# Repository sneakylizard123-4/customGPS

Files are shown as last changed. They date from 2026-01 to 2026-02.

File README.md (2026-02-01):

# customGPS
A custom GPS and compass board for 5" drones.

## How to use
connect to power. GPS uses UART and compass uses I2C.
solder capacitor to "cap here"

# Pictures
blender render:


PCB:


Schematic:


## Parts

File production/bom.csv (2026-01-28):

Designator | Footprint | Quantity | Value | LCSC Part #
C1, C3, C4, C6 | 0805 | 4 | 100nF
C2, C7, C8 | 0805 | 3 | 1uF
C5 | 0805 | 1 | 10nF
D1, D2 | 0603 | 2 | Status LED
FB1 | 0603 | 1 | BLM18AG601SN1D | BLM18AG601SN1D
J1 | SolderWirePad_1x01_SMD_1x2mm | 1 | C+
J2 | SolderWirePad_1x01_SMD_1x2mm | 1 | C-
J3 | U.FL_Molex_MCRF_73412-0110_Vertical | 1 | U_FL-R-SMT-1_10_ | U.FL-R-SMT-1(10)
J4 | Hirose_DF13-06P-1.25DS_1x06_P1.25mm_Horizontal | 1 | To FC
J6 | SolderWirePad_1x01_SMD_1x2mm | 1 | DRDY
L1 | 0805 | 1 | 10nH
R1 | 0805 | 1 | 10k
R2, R3 | 0805 | 2 | 47
R4 | 0805 | 1 | 100
R5, R8 | 0805 | 2 | 1K
R6, R7 | 0805 | 2 | 0
TP1 | TestPoint_Pad_1.0x1.0mm | 1 | SAFEBOOT
TP2 | TestPoint_Pad_1.0x1.0mm | 1 | TimePulse
U1 | ublox_NEO | 1 | NEO-M8N
U2 | LGA-12_2x2mm_P0.5mm | 1 | LIS3MDL
U3 | SOT-23-5 | 1 | TLV75733PDBV

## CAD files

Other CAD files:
blender/customGPS.blend

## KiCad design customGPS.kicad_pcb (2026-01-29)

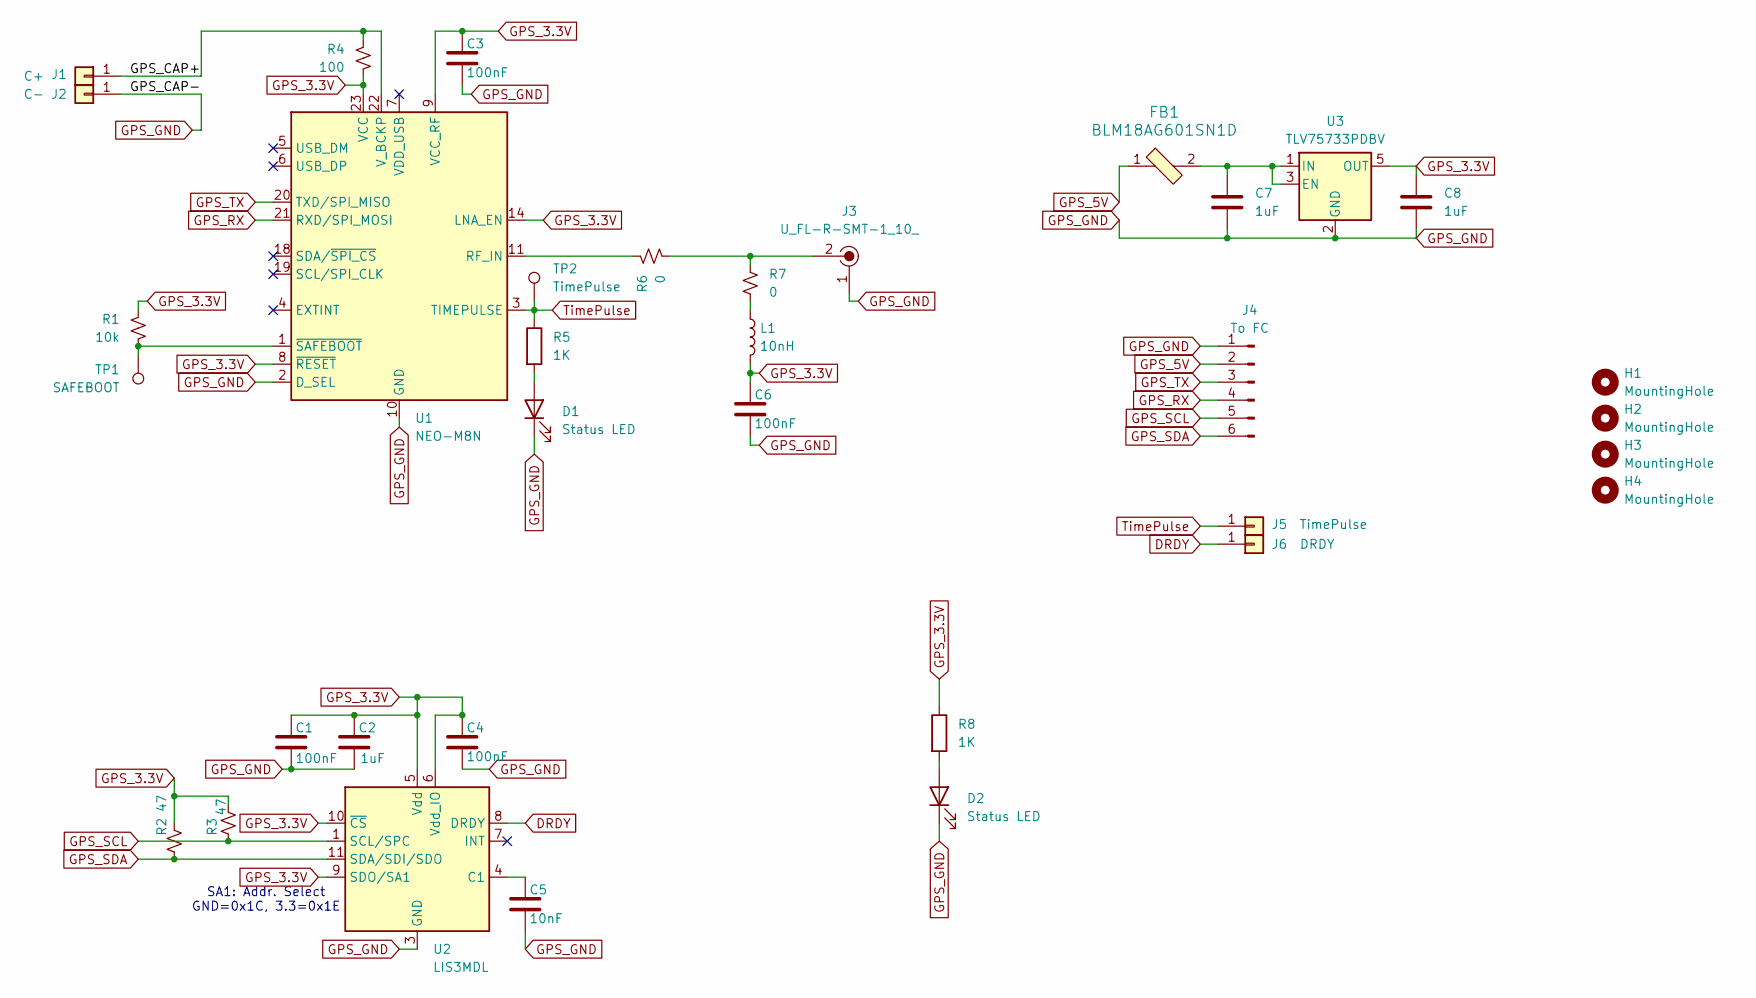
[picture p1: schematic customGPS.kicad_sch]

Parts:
C1, C3, C4, C6: 100nF; C_0805_2012Metric_Pad1.18x1.45mm_HandSolder
C2, C7, C8: 1uF; C_0805_2012Metric_Pad1.18x1.45mm_HandSolder
C5: 10nF; C_0805_2012Metric_Pad1.18x1.45mm_HandSolder
D1, D2: Status LED; LED_0603_1608Metric_Pad1.05x0.95mm_HandSolder
FB1: BLM18AG601SN1D; 0603; MPN BLM18AG601SN1D; Digi-Key_PN 490-1014-1-ND
H1, H2, H3, H4: MountingHole; MountingHole_3.2mm_M3
J1: C+; SolderWirePad_1x01_SMD_1x2mm
J2: C-; SolderWirePad_1x01_SMD_1x2mm
J3: U_FL-R-SMT-1_10_; U.FL_Molex_MCRF_73412-0110_Vertical; MPN U.FL-R-SMT-1(10); Digi-Key_PN H11891CT-ND
J4: To FC; Hirose_DF13-06P-1.25DS_1x06_P1.25mm_Horizontal
J5: TimePulse; SolderWirePad_1x01_SMD_1x2mm
J6: DRDY; SolderWirePad_1x01_SMD_1x2mm
L1: 10nH; L_0805_2012Metric_Pad1.05x1.20mm_HandSolder
R1: 10k; R_0805_2012Metric_Pad1.20x1.40mm_HandSolder
R2, R3: 47; R_0805_2012Metric_Pad1.20x1.40mm_HandSolder
R4: 100; R_0805_2012Metric_Pad1.20x1.40mm_HandSolder
R5, R8: 1K; R_0805_2012Metric_Pad1.20x1.40mm_HandSolder
R6, R7: 0; R_0805_2012Metric_Pad1.20x1.40mm_HandSolder
TP1: SAFEBOOT; TestPoint_Pad_1.0x1.0mm
TP2: TimePulse; TestPoint_Pad_1.0x1.0mm
U1: NEO-M8N; ublox_NEO
U2: LIS3MDL; LGA-12_2x2mm_P0.5mm
U3: TLV75733PDBV; SOT-23-5

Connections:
/GPS_CAP+: J1.1, R4.1, U1.22 (V_BCKP)
DRDY: J6.1, U2.8 (DRDY)
GPS_3.3V: C1.1, C2.1, C3.1, C4.1, C6.1, C8.1, L1.2, R1.1, R2.1, R3.2, R4.2, R8.1, U1.8 (~RESET), U1.9 (VCC_RF), U1.14 (LNA_EN), U1.23 (VCC), U2.5 (Vdd), U2.6 (Vdd_IO), U2.9 (SDO/SA1), U2.10 (~CS), U3.5 (OUT)
GPS_5V: FB1.1, J4.2
GPS_GND: C1.2, C2.2, C3.2, C4.2, C5.2, C6.2, C7.2, C8.2, D1.1 (K), D2.1 (K), J2.1, J3.1, J4.1, U1.2 (D_SEL), U1.10 (GND), U1.12 (GND), U1.13 (GND), U1.24 (GND), U2.2 (GND), U2.3 (GND), U2.12 (GND), U3.2 (GND)
GPS_RX: J4.4, U1.21 (RXD/SPI_MOSI)
GPS_SCL: J4.5, R3.1, U2.1 (SCL/SPC)
GPS_SDA: J4.6, R2.2, U2.11 (SDA/SDI/SDO)
GPS_TX: J4.3, U1.20 (TXD/SPI_MISO)
unnamed: D1.2 (A), R5.2
unnamed: D2.2 (A), R8.2
unnamed: J3.2, R6.2, R7.1
unnamed: L1.1, R7.2
unnamed: R6.1, U1.11 (RF_IN)
unnamed: R1.2, TP1.1, U1.1 (~SAFEBOOT)
unnamed: C5.1, U2.4 (C1)
unnamed: C7.1, FB1.2, U3.1 (IN), U3.3 (EN)
TimePulse: J5.1, R5.1, TP2.1, U1.3 (TIMEPULSE)

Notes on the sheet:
SA1: Addr. Select GND=0x1C, 3.3=0x1E

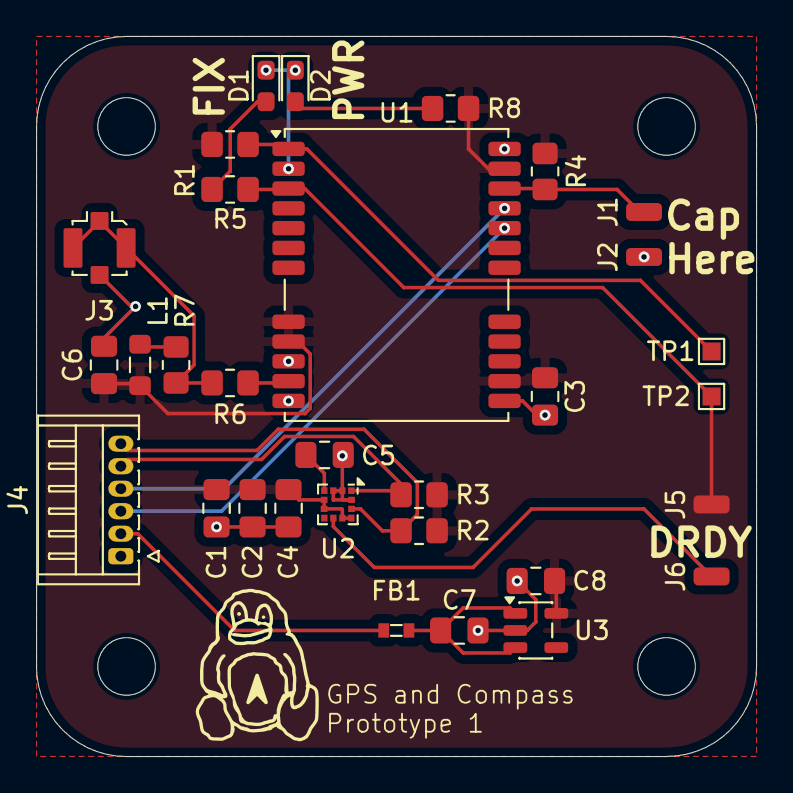
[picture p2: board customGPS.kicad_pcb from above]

Board: 2 copper layers, 40.0 x 40.0 mm, 35 parts (0 on the bottom side), 18 nets.

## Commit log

2026-01-28 add pcb3d export
2026-01-28 add blend file
    [customGPS.blend]
2026-01-28 Enhance README with images and formatting
    Added images for the PCB and schematic to the README.
2026-01-29 update pcb and fix drc errors
    [customGPS.kicad_pcb]
2026-02-01 Update README with capacitor soldering instructions
    Added instructions to solder capacitor to the documentation.
